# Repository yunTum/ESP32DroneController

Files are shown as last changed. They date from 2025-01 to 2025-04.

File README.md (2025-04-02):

# ESP32DroneController

## Debug Software


## Web Setting


## FlightAnalyzer


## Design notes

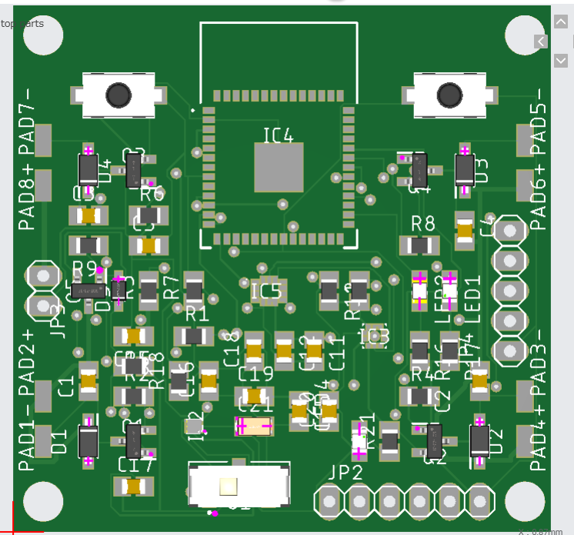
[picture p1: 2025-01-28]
schematic/ESPDroneV2/スクリーンショット 2025-01-21 234431.png

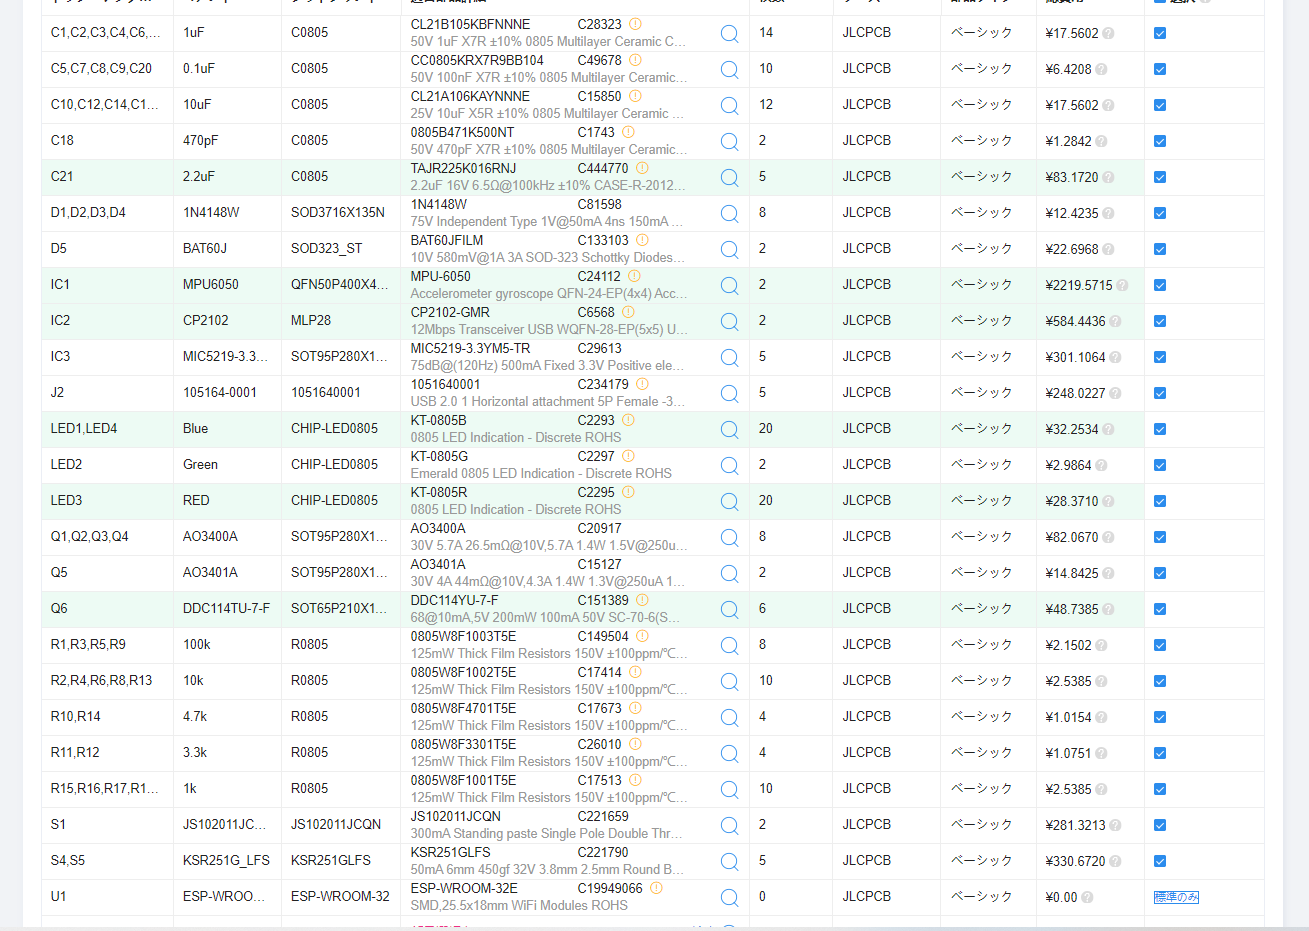
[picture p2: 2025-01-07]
schematic/esp32drone/スクリーンショット 2024-10-18 125452.png

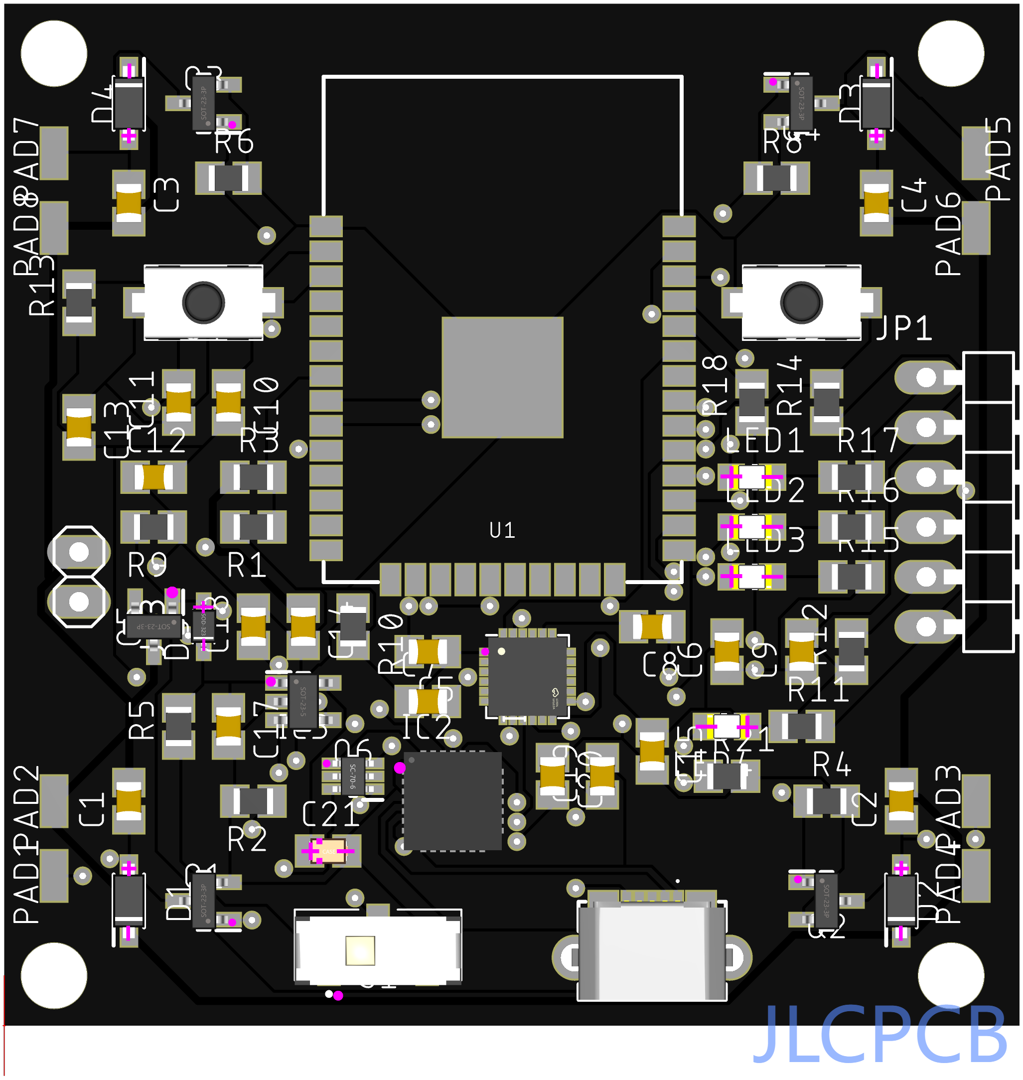
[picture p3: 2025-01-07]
schematic/esp32drone/capture-2024-10-16T03_43_27.196Z.png

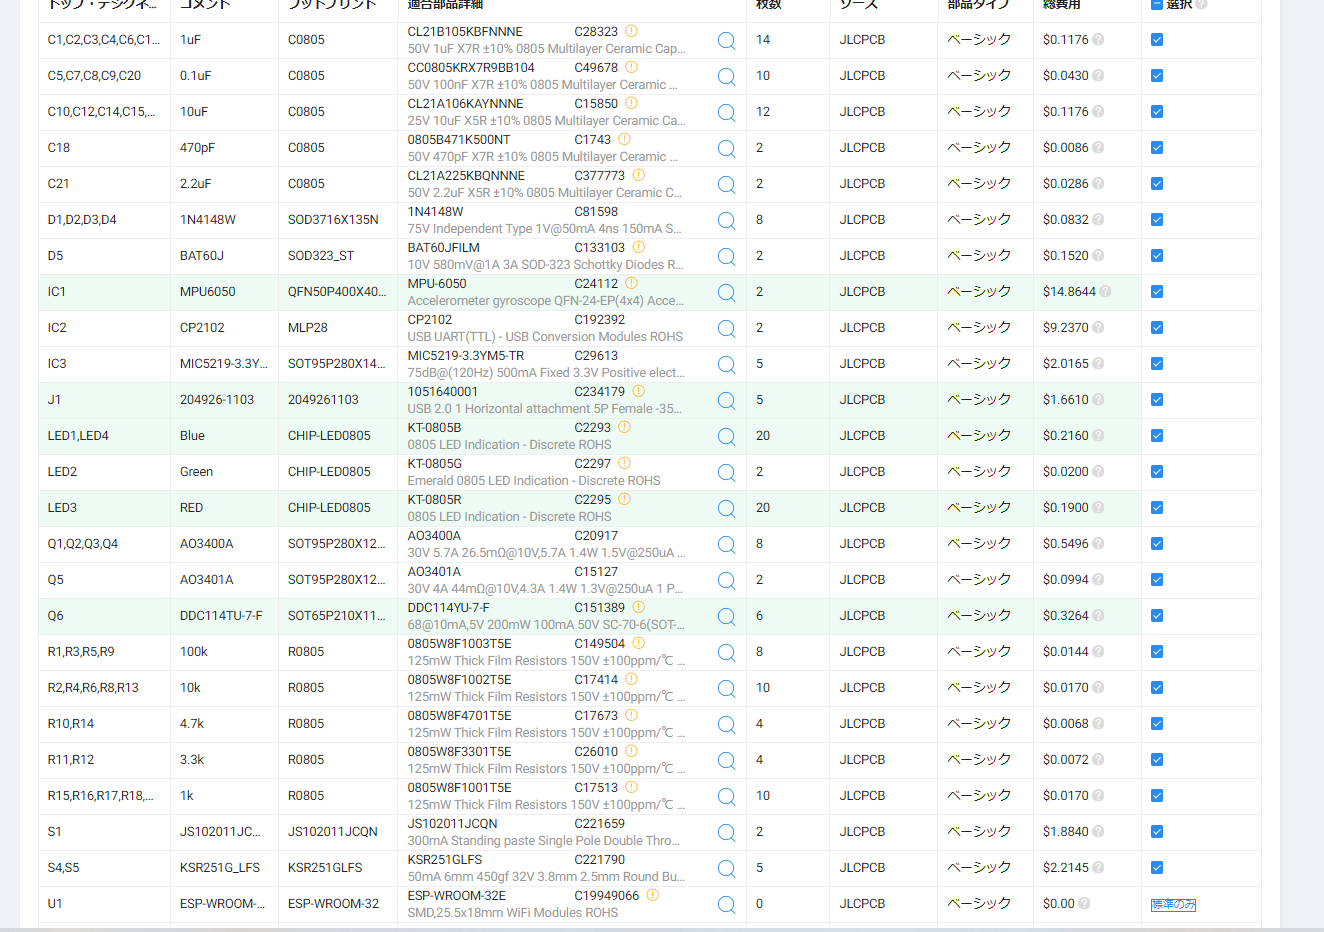
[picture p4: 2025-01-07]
schematic/esp32drone/スクリーンショット 2024-10-16 073514.png

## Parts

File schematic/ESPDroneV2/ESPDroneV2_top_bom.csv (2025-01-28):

Comment | Designator | Footprint | LCSC Part #
1N4148W | D1 D2 D3 D4 | SOD3716X135N
1k | R16 R17 R21 | R0805
1uF | C1 C2 C3 C4 C5 C11 C15 C17 C18 C19 | C0805
2.2uF | C21 | C0805
3.3k | R11 R12 | R0805
4.7k | R18 | R0805
10k | R2 R4 R6 R7 R8 | R0805
10uF | C14 C16 | C0805
100k | R1 R3 R5 R9 | R0805
100uF | C12 C20 | C0805
AO3400A | Q1 Q2 Q3 Q4 | SOT95P280X125-3N
AO3401A | Q5 | SOT95P280X125-3N
BAT60J | D5 | SOD323_ST
Blue | LED1 LED4 | CHIP-LED0805
ESP32-MINI-1-N4 | IC4 | ESP32MINI1N4
Green | LED2 | CHIP-LED0805
JS102011JCQN | S1 | JS102011JCQN
KSR251G_LFS | S2 S3 | KSR251GLFS
LPS22HHTR | IC3 | LPS22HHTR
LSM6DSLTR | IC5 | LSM6DSLTR
MOTOR1+ | PAD2+ | SMD1 27-2 54
MOTOR1- | PAD1- | SMD1 27-2 54
MOTOR2+ | PAD4+ | SMD1 27-2 54
MOTOR2- | PAD3- | SMD1 27-2 54
MOTOR3+ | PAD6+ | SMD1 27-2 54
MOTOR3- | PAD5- | SMD1 27-2 54
MOTOR4+ | PAD8+ | SMD1 27-2 54
MOTOR4- | PAD7- | SMD1 27-2 54
NCP176AMX330TCG | IC2 | NCP176AMX330TCG

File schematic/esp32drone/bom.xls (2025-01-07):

Comment | Designator | Footprint | JLCPCB Part #
1uF | C1,C2,C3,C4,C6,C11,C13,C16 | C0805 | C28323
DDC114TU-7-F | Q6 | SOT65P210X110-6N | C260942
56k | R7,R9,R13 | R0805 | C17756
Green | LED2 | CHIP-LED0805 | C84257
470pF | C18 | C0805 | C1743
MINI-USB-32005-201 | X1 | 32005-201 | C2681563
JS102011JCQN | S7 | JS102011JCQN | C221659
3.3k | R11,R12 | R0805 | C26010
RED | LED3 | CHIP-LED0805 | C84256
100k | R1,R3 | R0805 | C149504
10k | R2,R4,R6,R8 | R0805 | C17414
AO3401A | Q5 | SOT95P280X125-3N | C15127
Blue | LED1,LED4 | CHIP-LED0805 | C84259
AO3400A | Q1,Q2,Q3,Q4 | SOT95P280X125-3N | C344010
1k | R15,R16,R17,R18,R21 | R0805 | C17513
2.2nF | C8 | C0805 | C28260
10uF | C10,C12,C14,C15,C17,C19 | C0805 | C15850
4.7k | R10,R14 | R0805 | C17673
MPU6050 | IC1 | QFN50P400X400X95-25T265X275N | C24112
0.1uF | C5,C7,C9,C20 | C0805 | C49678
MIC5219-3.3YM5-TR | IC4 | SOT95P280X145-5N | C29613
BAT60J | D5 | SOD323_ST | C133103
ESP-WROOM-32 | U1 | ESP-WROOM-32 | C82899
CP2102 | IC2 | MLP28 | C192392
KSR251G_LFS | S4,S5 | KSR251GLFS | C221790
1N4148W | D1,D2,D3,D4 | SOD3716X135N | C81598

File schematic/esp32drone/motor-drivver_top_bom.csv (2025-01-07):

Comment | Designator | Footprint | LCSC Part #
0.1uF | C5 C7 C8 C9 C20 | C0805
1N4148W | D1 D2 D3 D4 | SOD3716X135N
1k | R15 R16 R17 R18 R21 | R0805
1uF | C1 C2 C3 C4 C6 C11 C13 | C0805
2.2uF | C21 | C0805
3.3k | R11 R12 | R0805
4.7k | R10 R14 | R0805
10k | R2 R4 R6 R8 R13 | R0805
10uF | C10 C12 C14 C15 C17 C19 | C0805
100k | R1 R3 R5 R9 | R0805
470pF | C18 | C0805
105164-0001 | J2 | 1051640001
AO3400A | Q1 Q2 Q3 Q4 | SOT95P280X125-3N
AO3401A | Q5 | SOT95P280X125-3N
BAT60J | D5 | SOD323_ST
Blue | LED1 LED4 | CHIP-LED0805
CP2102 | IC2 | MLP28
DDC114TU-7-F | Q6 | SOT65P210X110-6N
ESP-WROOM-32 | U1 | ESP-WROOM-32
Green | LED2 | CHIP-LED0805
JS102011JCQN | S1 | JS102011JCQN
KSR251G_LFS | S4 S5 | KSR251GLFS
MIC5219-3.3YM5-TR | IC3 | SOT95P280X145-5N
MOTOR1+ | PAD2 | SMD1 27-2 54
MOTOR1- | PAD1 | SMD1 27-2 54
MOTOR2+ | PAD4 | SMD1 27-2 54
MOTOR2- | PAD3 | SMD1 27-2 54
MOTOR3+ | PAD6 | SMD1 27-2 54
MOTOR3- | PAD5 | SMD1 27-2 54
MOTOR4+ | PAD8 | SMD1 27-2 54
MOTOR4- | PAD7 | SMD1 27-2 54
MPU6050 | IC1 | QFN50P400X400X95-25T265X275N
RED | LED3 | CHIP-LED0805

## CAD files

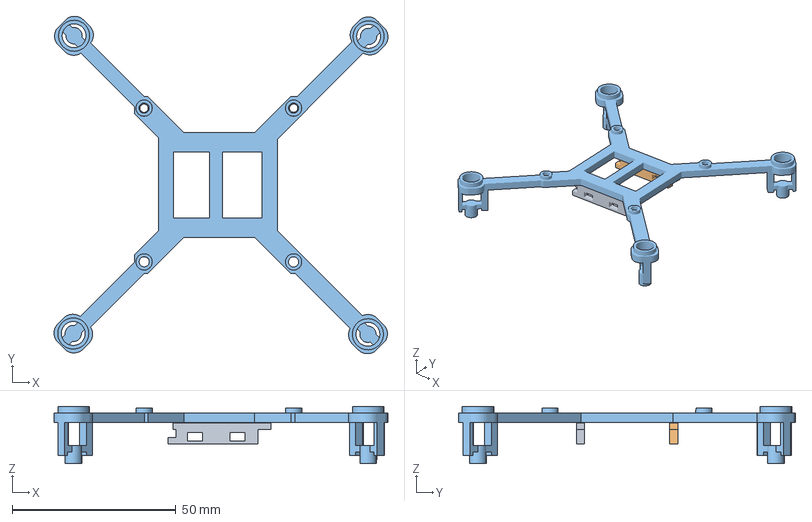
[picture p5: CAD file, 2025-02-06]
frame/ESPドローンフレームV6_SMALL v4.3mf
102.1 x 103.1 x 17.5 mm
ボディ36
ボディ59
ボディ86

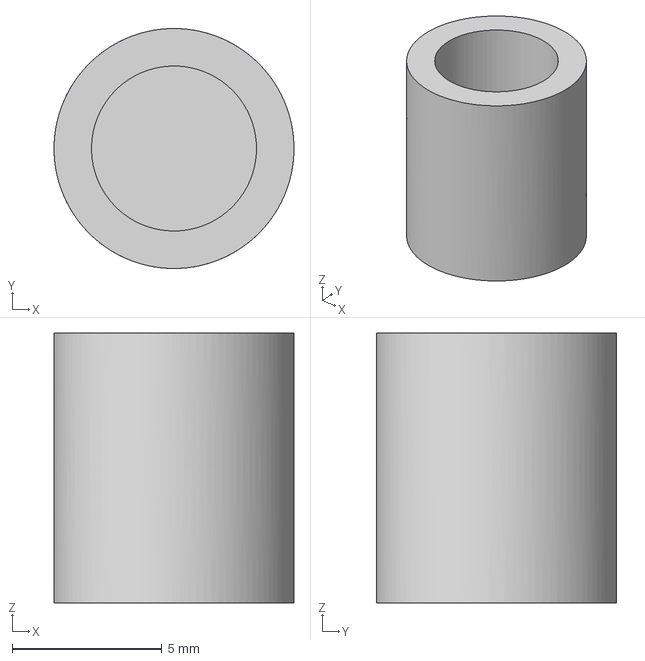
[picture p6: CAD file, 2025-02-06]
frame/offset_foot v2.3mf
8.00 x 8.00 x 9.00 mm

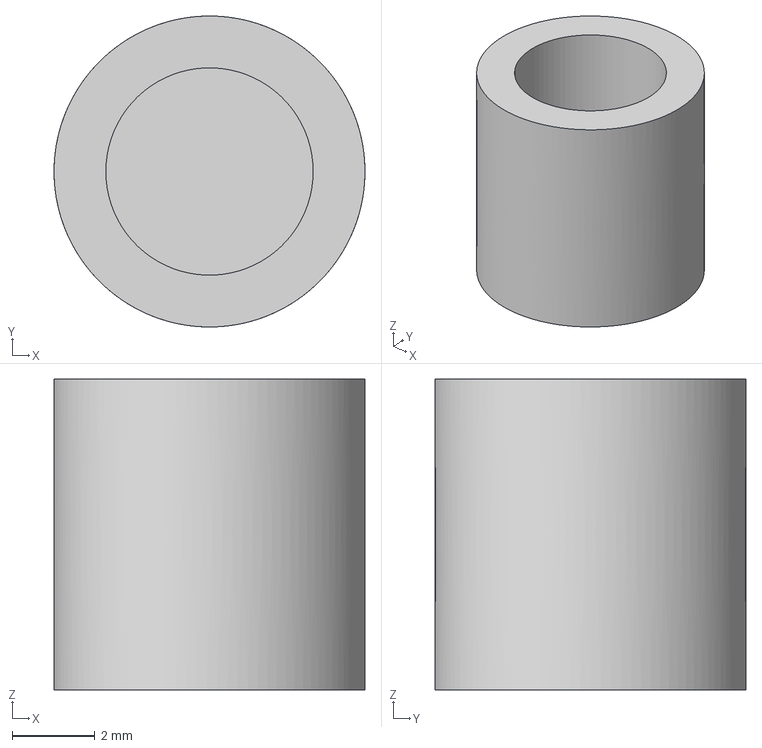
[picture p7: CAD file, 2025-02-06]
frame/offset_foot.3mf
7.50 x 7.50 x 7.50 mm

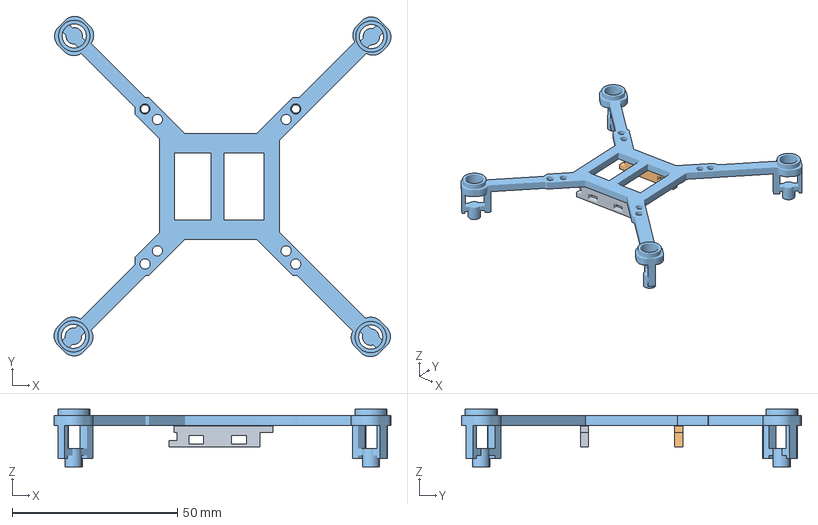
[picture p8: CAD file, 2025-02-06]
frame/ESPドローンV3フレーム v1.3mf
102.1 x 103.1 x 17.5 mm
ボディ36
ボディ59
ボディ86

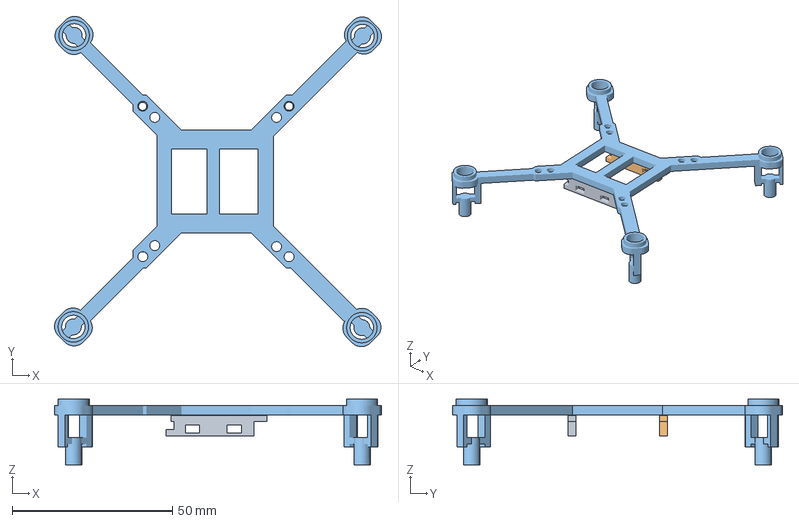
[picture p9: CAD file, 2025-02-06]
frame/ESPドローンV3フレーム v2.3mf
102.1 x 103.1 x 20.5 mm
ボディ36
ボディ59
ボディ86

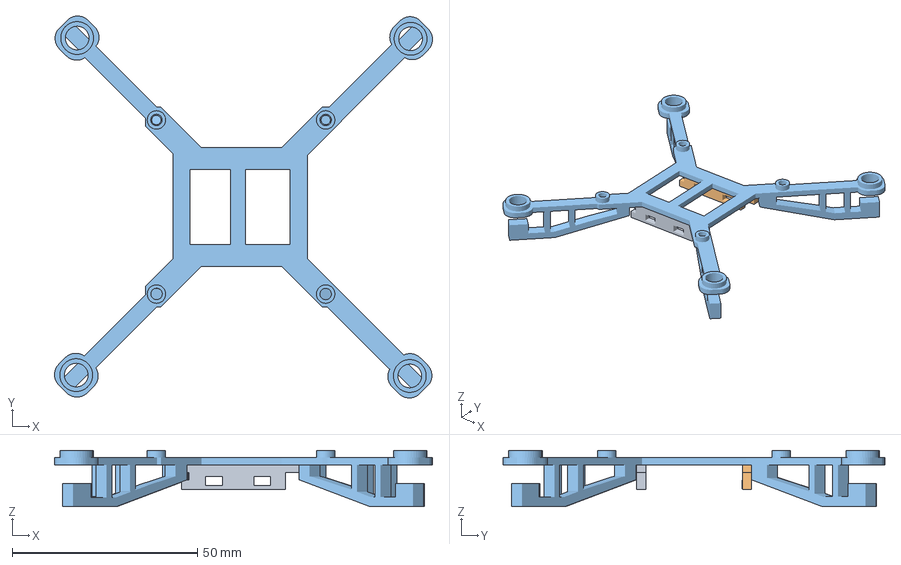
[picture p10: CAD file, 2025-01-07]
frame/ESPドローンフレームV5_SMALL v5.3mf
102.0 x 103.1 x 15.2 mm
ボディ36
ボディ59
ボディ86

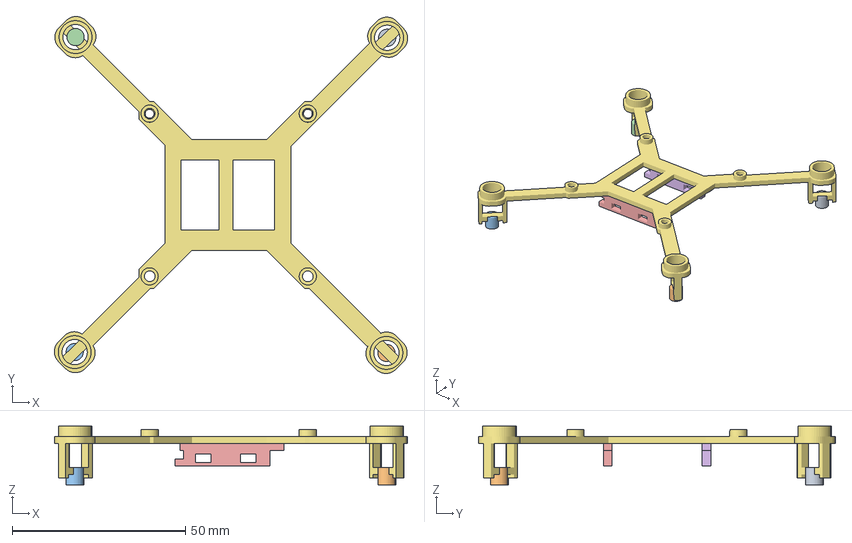
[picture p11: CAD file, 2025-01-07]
frame/ESPドローンフレームV6_SMALL v3.3mf
102.1 x 103.1 x 17.0 mm
ボディ107
ボディ108
ボディ109
ボディ110
ボディ36
ボディ59
ボディ86

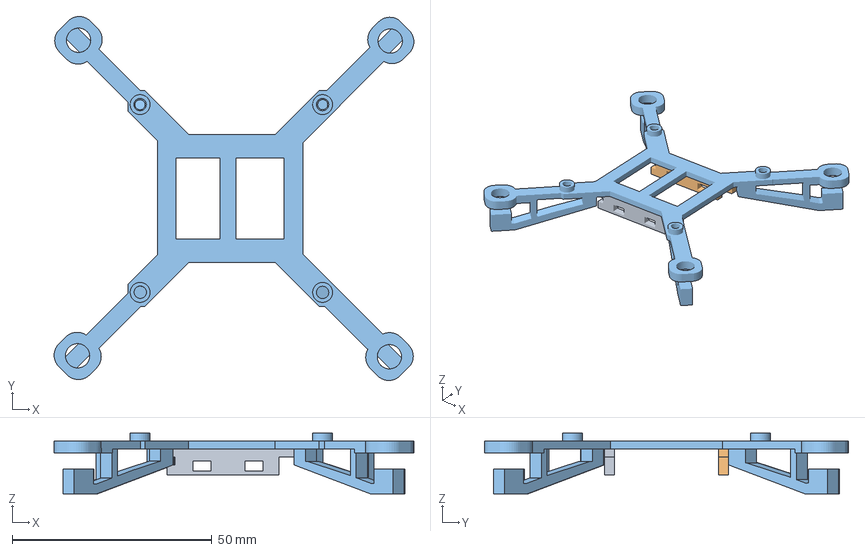
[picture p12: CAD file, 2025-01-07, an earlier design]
frame/ESPドローンフレームV5_SMALL v4.3mf
90.1 x 91.1 x 15.2 mm
ボディ36
ボディ59
ボディ62

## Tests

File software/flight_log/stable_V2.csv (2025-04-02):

timestamp | seqno | synctime | servo1 | servo2 | servo3 | servo4 | pid_roll | pid_pitch | pid_yaw | imu_roll | imu_pitch | imu_yaw | gyro_x | gyro_y | gyro_z | acc_x | acc_y | acc_z | battery | altitude | temperature | calculated_altitude
2025-04-03 00:18:51 | 78 | 41.539 | 0 | 0 | 0 | 0 | -0.05 | 0.05 | 0.00 | 0.06 | -0.06 | -0.03 | 0.00 | 0.00 | 0.00 | 0.00 | 0.00 | 40.95 | 3.47 | -0.16 | 26.30 | -10987.54
2025-04-03 00:18:51 | 85 | 53.829 | 0 | 0 | 0 | 0 | -0.05 | 0.05 | 0.00 | 0.06 | -0.06 | -0.03 | 0.00 | 0.00 | 0.00 | 0.00 | 0.00 | 40.93 | 3.47 | -0.08 | 26.30 | -27434.34
2025-04-03 00:18:51 | 86 | 8.774 | 0 | 0 | 0 | 0 | -0.05 | 0.05 | 0.00 | 0.06 | -0.06 | -0.03 | 0.00 | 0.00 | 0.00 | 0.00 | 0.00 | 40.93 | 3.47 | 0.16 | 26.30 | 32807.77
2025-04-03 00:18:52 | 87 | 29.254 | 0 | 0 | 0 | 0 | -0.05 | 0.05 | 0.00 | 0.06 | -0.06 | -0.03 | 0.00 | 0.00 | 0.00 | 0.00 | 0.00 | 40.93 | 3.47 | 0.28 | 26.29 | 5442.00
2025-04-03 00:18:52 | 88 | 49.734 | 0 | 0 | 0 | 0 | -0.05 | 0.05 | 0.00 | 0.06 | -0.06 | -0.03 | 0.00 | 0.00 | 0.00 | 0.00 | 0.00 | 40.91 | 3.47 | -0.75 | 26.30 | -21957.32
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

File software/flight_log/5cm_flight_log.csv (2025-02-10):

timestamp | seqno | servo1 | servo2 | servo3 | servo4 | pid_roll | pid_pitch | pid_yaw | imu_roll | imu_pitch | imu_yaw | gyro_x | gyro_y | gyro_z | acc_x | acc_y | acc_z | battery | altitude | temperature
2025-02-10 11:53:55 | 0 | 0 | 0 | 0 | 0 | 0.00 | 0.00 | 0.00 | 0.00 | 0.00 | 0.00 | 0.00 | 0.00 | 0.00 | 0.00 | 0.00 | 0.00 | 3.44 | 0.00 | 0.00
2025-02-10 11:53:55 | 1 | 0 | 0 | 0 | 0 | 0.00 | 0.00 | 0.00 | 0.00 | 0.00 | 0.00 | 0.00 | 0.00 | 0.00 | 0.00 | 0.00 | 0.00 | 3.40 | 0.00 | 0.00
2025-02-10 11:53:55 | 2 | 0 | 0 | 0 | 0 | 0.00 | 0.00 | 0.00 | 0.00 | 0.00 | 0.00 | 0.00 | 0.00 | 0.00 | 0.00 | 0.00 | 0.00 | 3.41 | 0.00 | 0.00
2025-02-10 11:53:55 | 3 | 0 | 0 | 0 | 0 | 0.00 | 0.00 | 0.00 | 0.00 | 0.00 | 0.00 | 0.00 | 0.00 | 0.00 | 0.00 | 0.00 | 0.00 | 3.41 | 0.00 | 0.00
2025-02-10 11:53:56 | 4 | 0 | 0 | 0 | 0 | 0.00 | 0.00 | 0.00 | 0.00 | 0.00 | 0.00 | 0.00 | 0.00 | 0.00 | 0.00 | 0.00 | 0.00 | 3.40 | 0.00 | 0.00
2025-02-10 11:53:56 | 7 | 0 | 0 | 0 | 0 | 0.00 | 0.00 | 0.00 | 0.00 | 0.00 | 0.00 | 0.00 | 0.00 | 0.00 | 0.00 | 0.00 | 0.00 | 3.41 | 0.00 | 0.00
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

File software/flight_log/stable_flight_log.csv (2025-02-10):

timestamp | seqno | servo1 | servo2 | servo3 | servo4 | pid_roll | pid_pitch | pid_yaw | imu_roll | imu_pitch | imu_yaw | gyro_x | gyro_y | gyro_z | acc_x | acc_y | acc_z | battery | altitude | temperature | calculated_altitude
2025-02-10 18:42:00 | 0 | 0 | 0 | 0 | 0 | 0.00 | 0.00 | 0.00 | 0.00 | 0.00 | 0.00 | 0.00 | 0.00 | 0.00 | 0.00 | 0.00 | 0.00 | 3.50 | 0.00 | 0.00 | 9245.58
2025-02-10 18:42:00 | 1 | 0 | 0 | 0 | 0 | 0.00 | 0.00 | 0.00 | 0.00 | 0.00 | 0.00 | 0.00 | 0.00 | 0.00 | 0.00 | 0.00 | 0.00 | 3.47 | 0.00 | 0.00 | 9242.97
2025-02-10 18:42:00 | 2 | 0 | 0 | 0 | 0 | 0.00 | 0.00 | 0.00 | 0.00 | 0.00 | 0.00 | 0.00 | 0.00 | 0.00 | 0.00 | 0.00 | 0.00 | 3.47 | 0.00 | 0.00 | 9217.43
2025-02-10 18:42:00 | 10 | 0 | 0 | 0 | 0 | 0.00 | 0.00 | 0.00 | 0.00 | 0.00 | 0.00 | 0.00 | 0.00 | 0.00 | 0.00 | 0.00 | 0.00 | 3.47 | 0.00 | 0.00 | 9215.71
2025-02-10 18:42:00 | 11 | 0 | 0 | 0 | 0 | 0.00 | 0.00 | 0.00 | 0.00 | 0.00 | 0.00 | 0.00 | 0.00 | 0.00 | 0.00 | 0.00 | 0.00 | 3.47 | 0.00 | 0.00 | 9206.49
2025-02-10 18:42:00 | 13 | 0 | 0 | 0 | 0 | 0.00 | 0.00 | 0.00 | 0.00 | 0.00 | 0.00 | 0.00 | 0.00 | 0.00 | 0.00 | 0.00 | 0.00 | 3.47 | 0.00 | 0.00 | 9205.38
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

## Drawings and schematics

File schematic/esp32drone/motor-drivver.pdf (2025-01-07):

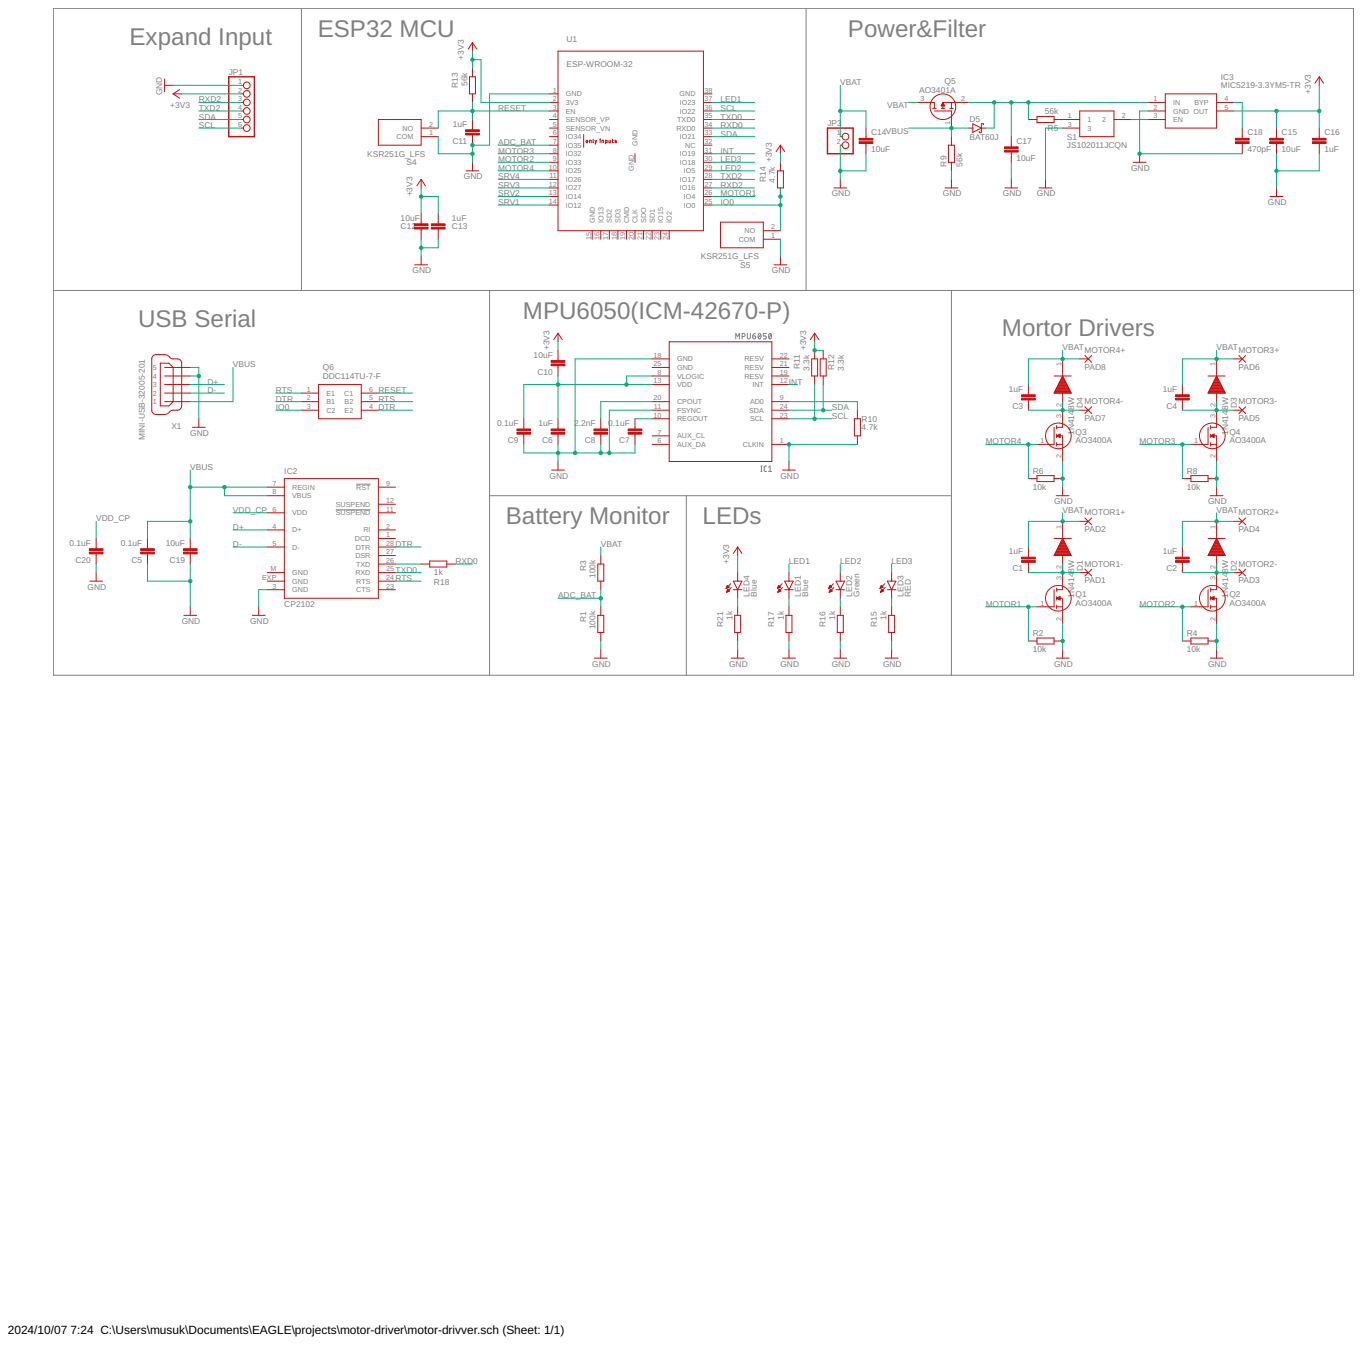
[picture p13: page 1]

2024/10/07 7:24 C:\Users\musuk\Documents\EAGLE\projects\motor-driver\motor-drivver.sch (Sheet: 1/1)

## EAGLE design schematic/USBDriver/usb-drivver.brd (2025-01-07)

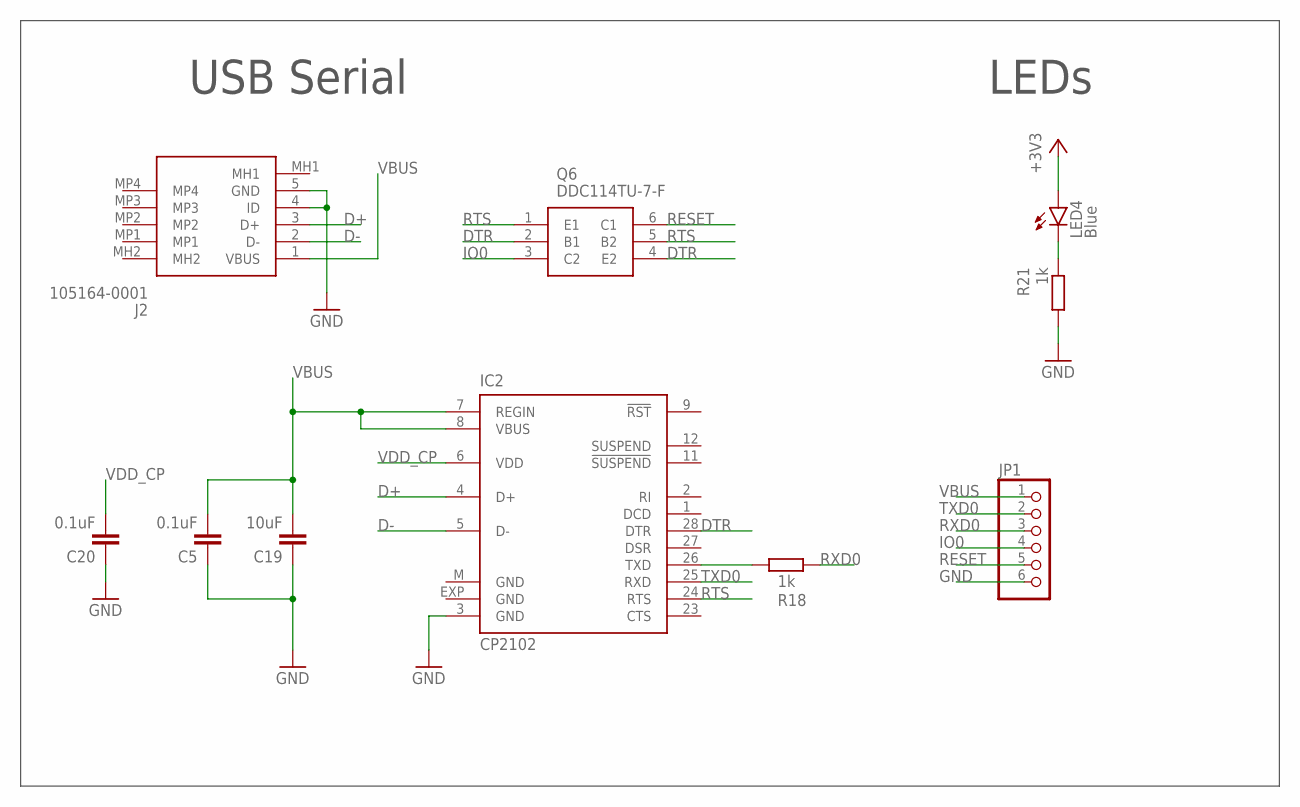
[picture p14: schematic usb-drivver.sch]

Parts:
C5, C20: 0.1uF; C0805
C19: 10uF; C0805
IC2: CP2102; MLP28
J2: 105164-0001; 1051640001
JP1: PINHD-1X6; 1X06
LED4: Blue; CHIP-LED0805
Q6: DDC114TU-7-F; SOT65P210X110-6N
R18, R21: 1k; R0805

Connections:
+3V3: LED4.A
D+: IC2.4 (D+), J2.3 (D+)
D-: IC2.5 (D-), J2.2 (D-)
DTR: IC2.28 (DTR), Q6.2 (B1), Q6.4 (E2)
GND: C5.1, C19.1, C20.1, IC2.3 (GND), IC2.EXP (GND), IC2.M (GND), J2.4 (ID), J2.5 (GND), JP1.6, R21.2
IO0: JP1.4, Q6.3 (C2)
unnamed: IC2.26 (TXD), R18.1
unnamed: LED4.C, R21.1
RESET: JP1.5, Q6.6 (C1)
RTS: IC2.24 (RTS), Q6.1 (E1), Q6.5 (B2)
RXD0: JP1.3, R18.2
TXD0: IC2.25 (RXD), JP1.2
VBUS: C5.2, C19.2, IC2.7 (REGIN), IC2.8 (VBUS), J2.1 (VBUS), JP1.1
VDD_CP: C20.2, IC2.6 (VDD)

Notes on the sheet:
USB Serial
LEDs

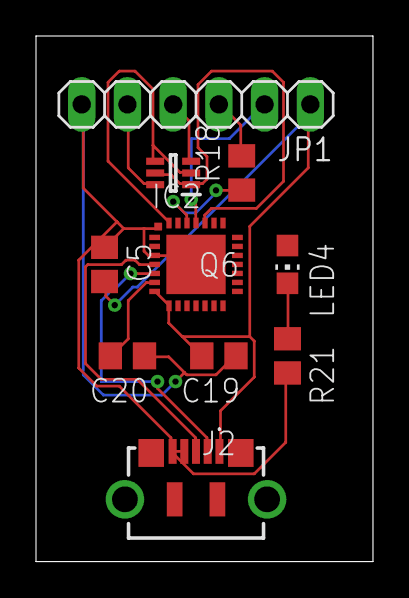
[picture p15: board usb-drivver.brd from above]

Board: 2 copper layers, 18.7 x 29.2 mm, 10 parts (0 on the bottom side), 13 nets.

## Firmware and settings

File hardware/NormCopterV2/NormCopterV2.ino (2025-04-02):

/*
UPDATE MARK 20240108
*/
#include <WiFi.h>
#include <WebServer.h>
#include "Arduino.h"
#include <EEPROM.h>
#include <esp_wifi.h>
#include <esp_bt.h>
#include <esp_pm.h>
#include <Wire.h>

WebServer server(80);

const char* ssid = "****************";
const char* password = "****************";

#define MINTHROTTLE 50
#define CALSTEPS 256 // gyro and acc calibration steps
enum ang { ROLL,PITCH,YAW };
#define THR 2 // thro position is rc_value array

#define EEPROM_SIZE 64
#define LED_YELLOW 23
#define LED_RED 18
#define LED_GREEN 5
#define ADC_BAT 35
#define LOW_VOLT 3.0
#define CS_PIN 27
String act_ip;

extern void initMot();
extern int16_t rcValue[];

#define LoopInterval 4 // minimum 2ms
const float dt = 0.001 * float(LoopInterval); //in sec 
unsigned long synctime;    

void setup() 
{
  Wire.begin(21, 22);  // SDA=21, SCL=22 (ESP32のデフォルトピン)
  // Wire.setClock(400000); // 400kHz I2C
  Wire.setClock(100000);  // 100kHzに設定

  EEPROM.begin(EEPROM_SIZE);  
  Serial.begin(115200);
  pinMode(ADC_BAT, INPUT);
  pinMode(LED_YELLOW, OUTPUT);
  // pinMode(LED_RED, OUTPUT);
  pinMode(LED_GREEN, OUTPUT);
  pinMode(CS_PIN, OUTPUT);
  digitalWrite(CS_PIN, HIGH);
  digitalWrite(LED_YELLOW, LOW);
  delay(3000);
  
  // Init Modules
  initMot();
  LSM6DSLTR_init();
  readacc();

  LPSHHTR_init();
  // Wi-Fi connection
  WiFi.mode(WIFI_STA);
  WiFi.setSortMethod(WIFI_CONNECT_AP_BY_SIGNAL);
  WiFi.setScanMethod(WIFI_ALL_CHANNEL_SCAN);
  WiFi.begin(ssid, password);
  while (WiFi.status() != WL_CONNECTED) 
  {
    delay(500);
    Serial.print(".");
  }
  Serial.println();
  act_ip = WiFi.localIP().toString().c_str();
  Serial.println(act_ip);

  delay(200);
  init_RC(); 
  server.on("/", handleCmd);
  server.begin();
  Serial.println("HTTP server started");
    
  Serial.println("T - Timing");
  Serial.println("R - RC");
  Serial.println("r - Raw RC");
  Serial.println("G - Gyro raw");
  Serial.println("g - Gyro filt");
  Serial.println("A - Accel raw");
  Serial.println("M - Madgwick");
  Serial.println("P - PID");
  Serial.println("S - Servo");
  Serial.println("B - Battery");
  Serial.println("H - LPS22HH");
  Serial.println("L - Logging");
  Serial.println("W - PID Settings");

  synctime = millis() + LoopInterval;
  digitalWrite(LED_GREEN, LOW);
  // digitalWrite(LED_YELLOW, LOW);
}

bool armed, fmode, led, calibrateRequest;

float GyroX,GyroY,GyroZ;
float AccX, AccY, AccZ;

extern int16_t gyroADC[3];
extern int16_t accADC[3];
extern float roll_IMU, pitch_IMU, yaw_IMU;
extern float roll_PID, pitch_PID, yaw_PID;
extern float roll_des, pitch_des, yaw_des;
extern float roll_rc, pitch_rc, yaw_rc;
// extern float throttle;
extern int16_t axisPID[3];
extern uint16_t servo[];

extern float pressure, temperature, altitude;

unsigned long oldT;
float B_gyro = 0.1;
char debugvalue;
float battery_vol = 0.0;
int counter = 0;
int sendInterval = 20;

bool isHeader = true;
const int LOG_INTERVAL = 20; // 何回のループに1回ログを取るか
int logCounter = 0;
bool isDetailLog = false;

extern float Kp_rate, Ki_rate, Kd_rate;
extern float Kp_yaw, Ki_yaw, Kd_yaw;
extern float Kp_ang, Ki_ang, Kd_ang;
extern float Kp_ayw, Ki_ayw, Kd_ayw;

void loop() 

{ 
  float gx,gy,gz;
  battery_vol = getBattery();
  if (debugvalue == 'B') showBatteryVol(battery_vol);
  
  // parser part
  if (Serial.available()) 
  {
    char ch = Serial.read();
    if (ch != 10) debugvalue = ch;
  }
  if (debugvalue == 'T') Serial.println(micros() - oldT);
  
  server.handleClient();
  while (millis() < synctime) delay(1);
  synctime += LoopInterval;
  
  if (debugvalue == 'T') oldT = micros();
  
  //des -> thr 0..+300; ang -90..+90
  rcvalCyclic();

  if (debugvalue == 'R') 
    Serial.printf("%4.0f %4.0f %4.0f  %d  %d  %d  %d\n", roll_rc, pitch_rc, yaw_rc, armed, fmode, led, calibrateRequest);  
  
  roll_des  = roll_rc;
  pitch_des = pitch_rc;
  yaw_des   = yaw_rc;
  
  if (calibrateRequest) {
    calibrateRequest = false;
    Serial.println("Calibrate Request");
    calibrate();
  }
  
  GyroAcc_getADC(); // 550us instead of 680us

  // gx = float(gyroADC[0]); 
  // gy = float(gyroADC[1]); 
  // gz = float(gyroADC[2]); 

  // GyroX = gx;
  // GyroY = gy;
  // GyroZ = gz;

  // // 1g=4096 -> 0.000244
  // AccX = float(accADC[0]);  
  // AccY = float(accADC[1]);  
  // AccZ = float(accADC[2]);

  if (debugvalue == 'G') 
    Serial.printf("%4d %4d %4d \n", gyroADC[0], gyroADC[1], gyroADC[2]);
  if (debugvalue == 'A') 
    Serial.printf("%5d %5d %5d \n", accADC[0], accADC[1], accADC[2]);
  getLPS22HH();

  if (debugvalue == 'H') 
    Serial.printf("Pressure: %6.2f Temp: %5.2f Alt: %6.2f \n", pressure, temperature, altitude);

  if (debugvalue == 'g') 
    Serial.printf("%4.0f %4.0f %4.0f \n", GyroX, GyroY, GyroZ);
  if (debugvalue == 'a') 
    Serial.printf("%4.0f %4.0f %4.0f \n", AccX, AccY, AccZ);

  Madgwick6DOF(GyroX,GyroY,GyroZ,AccX,AccY,AccZ,dt);
  if (debugvalue == 'M') 
    Serial.printf("%4.0f %4.0f %4.0f \n", roll_IMU, pitch_IMU, yaw_IMU);

  // fmode = true; // test
  if (fmode) {
    controlANG();
  } else {
    controlStable();
  }
  controlRATE();
  
  if (led) digitalWrite(LED_YELLOW, HIGH);
  else      digitalWrite(LED_YELLOW, LOW);

  if (debugvalue == 'P') Serial.printf("%4.0f %4.0f %4.0f \n", roll_PID, pitch_PID, yaw_PID);

  axisPID[ROLL]  = 10.0*roll_PID;
  axisPID[PITCH] = 10.0*pitch_PID;
  axisPID[YAW]   = 10.0*yaw_PID;
  if (counter == sendInterval) {
    sendDroneData();
    counter = 0;
  }

  // ロギング開始/停止のコマンドを追加
  if (debugvalue == 'L') {
    logCounter = 0;
    if(isHeader) {
      // ヘッダー行を送信

      Serial.println("DATA,gyroADC_X,gyroADC_Y,gyroADC_Z,accADC_X,accADC_Y,accADC_Z,GyroX,GyroY,GyroZ,AccX,AccY,AccZ,roll_IMU,pitch_IMU,yaw_IMU,roll_PID,pitch_PID,yaw_PID");
    }
    isHeader = false;
    // データロギング
    if(logCounter++ % LOG_INTERVAL == 0) {
      if (isDetailLog) {
        Serial.printf("DATA,%d,%d,%d,%d,%d,%d,%.2f,%.2f,%.2f,%.2f,%.2f,%.2f,%.2f,%.2f,%.2f,%.2f,%.2f,%.2f,%.2f\n",
          gyroADC[0], gyroADC[1], gyroADC[2],
          accADC[0], accADC[1], accADC[2],
          GyroX, GyroY, GyroZ,
          AccX, AccY, AccZ,
          roll_IMU, pitch_IMU, yaw_IMU,
          roll_PID, pitch_PID, yaw_PID);
      }
      else {
        Serial.printf("%.2f,%.2f,%.2f,%.2f,%.2f,%.2f\n",
          GyroX, GyroY, GyroZ,
          roll_PID, pitch_PID, yaw_PID);
      }
    }
  }

  if (debugvalue == 'W') {
      Serial.println("--------------------------------");
      Serial.println("Rate Settings");
      Serial.println("Kp_rate: " + String(Kp_rate));
      Serial.println("Ki_rate: " + String(Ki_rate));
      Serial.println("Kd_rate: " + String(Kd_rate));
      Serial.println("Yaw Settings");
      Serial.println("Kp_yaw: " + String(Kp_yaw));
      Serial.println("Ki_yaw: " + String(Ki_yaw));
      Serial.println("Kd_yaw: " + String(Kd_yaw));
      Serial.println("Ang Settings");
      Serial.println("Kp_ang: " + String(Kp_ang));
      Serial.println("Ki_ang: " + String(Ki_ang));
      Serial.println("Kd_ang: " + String(Kd_ang));
      Serial.println("Ang-Yaw Settings");
      Serial.println("Kp_ayw: " + String(Kp_ayw));
      Serial.println("Ki_ayw: " + String(Ki_ayw));
      Serial.println("Kd_ayw: " + String(Kd_ayw));
      Serial.println("--------------------------------");
      
      debugvalue = ' ';
  }

  counter++;
  mix();
  if (debugvalue == 'S') Serial.printf("%4d %4d %4d %4d\n", servo[0], servo[1], servo[2], servo[3]);
  // calib only !
  /*
  /**/
  // if (LOW_VOLT > battery_vol) {
  //   // digitalWrite(LED_GREEN, LOW);
  //   digitalWrite(LED_RED, HIGH);
  //   servo[0] = 0; servo[1] = 0; servo[2] = 0; servo[3] = 0; 
  // } else {
  //   // digitalWrite(LED_GREEN, HIGH);
  //   digitalWrite(LED_RED, LOW);
  // }
  writeMot();
}

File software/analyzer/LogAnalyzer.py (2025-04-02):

import pandas as pd
import matplotlib.pyplot as plt
import numpy as np
from pathlib import Path
import matplotlib.dates as mdates
from datetime import datetime
from PyQt5.QtWidgets import (QApplication, QMainWindow, QWidget, QVBoxLayout, 
                           QHBoxLayout, QPushButton, QLabel, QFileDialog, 
                           QComboBox, QMessageBox, QScrollArea, QTabWidget)
from PyQt5.QtCore import Qt
from matplotlib.backends.backend_qt5agg import FigureCanvasQTAgg as FigureCanvas
import sys

def analyze_log(file_path):
    # CSVファイルを読み込む
    df = pd.read_csv(file_path)
    
    # 基本的な統計情報を表示
    print("\n基本統計情報:")
    print(df.describe())
    
    # プロットの設定
    plt.rcParams['figure.figsize'] = [12, 6]
    plt.rcParams['grid.alpha'] = 0.3
    plt.rcParams['grid.color'] = '#cccccc'
    
    # IMUの角度データをプロット
    plt.figure()
    plt.plot(df['roll_IMU'], label='Roll')
    plt.plot(df['pitch_IMU'], label='Pitch')
    plt.plot(df['yaw_IMU'], label='Yaw')
    plt.title('IMU Angles')
    plt.xlabel('Sample')
    plt.ylabel('Angle (deg)')
    plt.legend()
    plt.grid(True)
    
    # PIDの出力をプロット
    plt.figure()
    plt.plot(df['roll_PID'], label='Roll PID')
    plt.plot(df['pitch_PID'], label='Pitch PID')
    plt.plot(df['yaw_PID'], label='Yaw PID')
    plt.title('PID Outputs')
    plt.xlabel('Sample')
    plt.ylabel('Output')
    plt.legend()
    plt.grid(True)
    
    # ジャイロデータをプロット
    plt.figure()
    plt.plot(df['GyroX'], label='X')
    plt.plot(df['GyroY'], label='Y')
    plt.plot(df['GyroZ'], label='Z')
    plt.title('Gyro Data')
    plt.xlabel('Sample')
    plt.ylabel('Angular Velocity (deg/s)')
    plt.legend()
    plt.grid(True)
    
    # 加速度データをプロット
    plt.figure()
    plt.plot(df['AccX'], label='X')
    plt.plot(df['AccY'], label='Y')
    plt.plot(df['AccZ'], label='Z')
    plt.title('Accelerometer Data')
    plt.xlabel('Sample')
    plt.ylabel('Acceleration (m/s²)')
    plt.legend()
    plt.grid(True)
    
    # 全てのグラフを表示
    plt.show()
    
    # 追加の統計情報
    print("\nIMU角度の平均値:")
    print(f"Roll: {df['roll_IMU'].mean():.2f}°")
    print(f"Pitch: {df['pitch_IMU'].mean():.2f}°")
    print(f"Yaw: {df['yaw_IMU'].mean():.2f}°")
    
    print("\nPID出力の標準偏差:")
    print(f"Roll: {df['roll_PID'].std():.2f}")
    print(f"Pitch: {df['pitch_PID'].std():.2f}")
    print(f"Yaw: {df['yaw_PID'].std():.2f}")

def analyze_phase(df):
    # IMUとPIDの相関を計算
    roll_corr = np.correlate(df['roll_IMU'], df['roll_PID'], mode='full')
    pitch_corr = np.correlate(df['pitch_IMU'], df['pitch_PID'], mode='full')
    yaw_corr = np.correlate(df['yaw_IMU'], df['yaw_PID'], mode='full')
    
    # IMUとPIDの比較プロット（正規化して表示）
    plt.figure(figsize=(15, 15))  # サイズを大きくして4つのサブプロットを配置
    
    # Roll
    plt.subplot(3, 1, 1)
    roll_imu_norm = df['roll_IMU'] / df['roll_IMU'].abs().max()
    roll_pid_norm = df['roll_PID'] / df['roll_PID'].abs().max()
    gyro_x_norm = df['GyroX'] / df['GyroX'].abs().max()
    plt.plot(gyro_x_norm, label='Gyro X (normalized)')
    # plt.plot(roll_imu_norm, label='Roll IMU (normalized)')
    plt.plot(roll_pid_norm, label='Roll PID (normalized)')

    # plt.plot(roll_imu_norm + roll_pid_norm, label='Combined', alpha=0.5)
    plt.plot(gyro_x_norm + roll_pid_norm, label='Combined', alpha=0.5)
    # plt.title('Roll: IMU vs PID (Normalized)')
    plt.title('Roll: Gyro X vs PID (Normalized)')

    plt.legend()
    plt.grid(True)
    
    # Pitch
    plt.subplot(3, 1, 2)
    pitch_imu_norm = df['pitch_IMU'] / df['pitch_IMU'].abs().max()
    pitch_pid_norm = df['pitch_PID'] / df['pitch_PID'].abs().max()
    gyro_y_norm = df['GyroY'] / df['GyroY'].abs().max()

    plt.plot(gyro_y_norm, label='Gyro Y (normalized)')
    # plt.plot(pitch_imu_norm, label='Pitch IMU (normalized)')
    plt.plot(pitch_pid_norm, label='Pitch PID (normalized)')
    plt.plot(gyro_y_norm + pitch_pid_norm, label='Combined', alpha=0.5)

    # plt.plot(pitch_imu_norm + pitch_pid_norm, label='Combined', alpha=0.5)
    # plt.title('Pitch: IMU vs PID (Normalized)')
    plt.title('Pitch: Gyro Y vs PID (Normalized)')
    plt.legend()
    plt.grid(True)
    

    # Yaw
    plt.subplot(3, 1, 3)
    yaw_imu_norm = df['yaw_IMU'] / df['yaw_IMU'].abs().max()
    yaw_pid_norm = df['yaw_PID'] / df['yaw_PID'].abs().max()
    gyro_z_norm = df['GyroZ'] / df['GyroZ'].abs().max()
    plt.plot(gyro_z_norm, label='Gyro Z (normalized)')

    # plt.plot(yaw_imu_norm, label='Yaw IMU (normalized)')
    plt.plot(yaw_pid_norm, label='Yaw PID (normalized)')
    plt.plot(gyro_z_norm + yaw_pid_norm, label='Combined', alpha=0.5)
    # plt.plot(yaw_imu_norm + yaw_pid_norm, label='Combined', alpha=0.5)

    # plt.title('Yaw: IMU vs PID (Normalized)')
    plt.title('Yaw: Gyro Z vs PID (Normalized)')
    plt.legend()
    plt.grid(True)
    

    # # 合成波形の比較
    # plt.subplot(4, 1, 4)
    # plt.plot(roll_imu_norm + roll_pid_norm, label='Roll Combined', alpha=0.7)
    # plt.plot(pitch_imu_norm + pitch_pid_norm, label='Pitch Combined', alpha=0.7)
    # plt.plot(yaw_imu_norm + yaw_pid_norm, label='Yaw Combined', alpha=0.7)
    # plt.title('Combined Waveforms Comparison')
    # plt.legend()
    # plt.grid(True)
    
    plt.tight_layout()
    plt.show()
    
    # 相関係数と合成波形の統計を計算
    print("\nIMUとPIDの相関係数（-1に近いほど良い）:")
    print(f"Roll: {df['GyroX'].corr(df['roll_PID']):.3f}")
    print(f"Pitch: {df['GyroY'].corr(df['pitch_PID']):.3f}")
    print(f"Yaw: {df['GyroZ'].corr(df['yaw_PID']):.3f}")

    print("\n合成波形の統計:")
    print("Roll合成波形の標準偏差:", (gyro_x_norm + roll_pid_norm).std().round(3))
    print("Pitch合成波形の標準偏差:", (gyro_y_norm + pitch_pid_norm).std().round(3))
    print("Yaw合成波形の標準偏差:", (gyro_z_norm + yaw_pid_norm).std().round(3))
    
    # 位相差の評価
    def calculate_phase_difference(imu, pid):
        correlation = np.correlate(imu, pid, mode='full')
        max_corr_index = np.argmax(np.abs(correlation))
        phase_diff = max_corr_index - len(imu)
        return phase_diff
    
    print("\n位相差（サンプル数）:")
    print(f"Roll: {calculate_phase_difference(gyro_x_norm, roll_pid_norm)}")
    print(f"Pitch: {calculate_phase_difference(gyro_y_norm, pitch_pid_norm)}")
    print(f"Yaw: {calculate_phase_difference(gyro_z_norm, yaw_pid_norm)}")
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

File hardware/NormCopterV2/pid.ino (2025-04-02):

float Kp_rate = 0.20;    //P-gain - rate mode
float Ki_rate = 0.01;    //I-gain - rate mode
float Kd_rate = 0.01;   //D-gain - rate mode 
float Kp_yaw  = 0.19;    //Yaw P-gain
float Ki_yaw  = 0.01;    //Yaw I-gain
float Kd_yaw  = 0.02;    //Yaw D-gain 

float Kp_ang  = 0.60;    //Ang P-gain
float Ki_ang  = 0.01;    //Ang I-gain
float Kd_ang  = 0.01;    //Ang D-gain
float Kp_ayw  = 0.20;    //Ang Yaw P-gain
float Ki_ayw  = 0.01;    //Ang Yaw I-gain
float Kd_ayw  = 0.07;    //Ang Yaw D-gain

float thro_des, roll_des, pitch_des, yaw_des; // RC input 0 to 1
float roll_rate_des, pitch_rate_des, yaw_rate_des; // Desired rate commands
float error_roll, integral_roll, integral_roll_prev, derivative_roll;
float error_pitch,integral_pitch,integral_pitch_prev,derivative_pitch;
float error_yaw,  integral_yaw,  integral_yaw_prev,  derivative_yaw;
float error_roll_prev, error_pitch_prev, error_yaw_prev;
float GyroX_prev, GyroY_prev, GyroZ_prev;
float integral_ang_roll,  integral_ang_roll_prev;
float integral_ang_pitch, integral_ang_pitch_prev;
float integral_ang_yaw,   integral_ang_yaw_prev;

float roll_PID = 0;
float pitch_PID = 0;
float yaw_PID = 0;

float i_limit = 5.0; 
extern int16_t rcValue[];

float pid_limit = 50;


// Stableモード用のPIDゲイン
// float Kp_stable = 1.3;     // 水平維持用の比例ゲイン
// float Ki_stable = 0.04;    // 水平維持用の積分ゲイン
// float Kd_stable = 0.02;    // 水平維持用の微分ゲイン
float Kp_stable = 0.14;     // 水平維持用の比例ゲイン
float Ki_stable = 0.01;    // 水平維持用の積分ゲイン
float Kd_stable = 0.00;    // 水平維持用の微分ゲイン
// float Kp_stable = 1.46;     // 水平維持用の比例ゲイン
// float Ki_stable = 0.40;    // 水平維持用の積分ゲイン
// float Kd_stable = 0.20;    // 水平維持用の微分ゲイン

// Stableモード用の積分項
float integral_stable_roll = 0;
float integral_stable_pitch = 0;
float prev_stable_roll_error = 0;
float prev_stable_pitch_error = 0;

#define MAX_ANGLE 25.0     // 最大傾斜角（度）
#define STABLE_I_LIMIT 10.0 // 積分項の制限

float filtered_roll_IMU = 0;
float filtered_pitch_IMU = 0;
float filtered_yaw_IMU = 0;

#define ANGLE_FILTER 0.95  // 角度フィルタの係数
#define D_FILTER_STABLE 0.8    // 微分項用フィルター係数
#define D_FILTER_RATE 0.8    // 微分項用フィルター係数
#define FILTER_GAIN 0.95    // フィルター係数

void controlStable() 
{
  // 角度のフィルタリング
  // filtered_roll_IMU = filtered_roll_IMU * ANGLE_FILTER + roll_IMU * (1 - ANGLE_FILTER);
  // filtered_pitch_IMU = filtered_pitch_IMU * ANGLE_FILTER + pitch_IMU * (1 - ANGLE_FILTER);

  // ロール角の制御（水平に戻す）
  float roll_error = 0 - roll_IMU;  // 目標角度は0度（水平）
  integral_stable_roll += roll_error * dt;
  integral_stable_roll = constrain(integral_stable_roll, -STABLE_I_LIMIT, STABLE_I_LIMIT);
  float roll_D = (roll_error - prev_stable_roll_error) / dt;
  // roll_D = roll_D * (1 - D_FILTER_STABLE) + prev_roll_D * D_FILTER_STABLE;

  // スティック入力との組み合わせ
  float stick_roll = roll_rc * MAX_ANGLE;  // スティック入力を角度に変換
  stick_roll = 0;
  roll_des = stick_roll + (Kp_stable * roll_error + 
                          Ki_stable * integral_stable_roll + 
                          Kd_stable * roll_D);
  
  // ピッチ角の制御（水平に戻す）
  float pitch_error = 0 - pitch_IMU;  // 目標角度は0度（水平）
  integral_stable_pitch += pitch_error * dt;
  integral_stable_pitch = constrain(integral_stable_pitch, -STABLE_I_LIMIT, STABLE_I_LIMIT);
  float pitch_D = (pitch_error - prev_stable_pitch_error) / dt;
  // pitch_D = pitch_D * (1 - D_FILTER_STABLE) + prev_pitch_D * D_FILTER_STABLE;

  // スティック入力との組み合わせ
  float stick_pitch = pitch_rc * MAX_ANGLE;  // スティック入力を角度に変換
  stick_pitch = 0;
  pitch_des = stick_pitch + (Kp_stable * pitch_error + 
                            Ki_stable * integral_stable_pitch + 
                            Kd_stable * pitch_D);
                            
  // ヨー制御（通常のレートモード）
  // yaw_des = yaw_rc * 180.0;  // ヨーレートの目標値（度/秒）
  yaw_des = 0;
  
  // 前回値の保存
  prev_stable_roll_error = roll_error;
  prev_stable_pitch_error = pitch_error;
  
  // スロットルが低い場合は積分項をリセット
  if (rcValue[THR] < MINTHROTTLE) {
    integral_stable_roll = 0;
    integral_stable_pitch = 0;
  }
  
  // 角度制限
  // roll_des = constrain(roll_des, -MAX_ANGLE, MAX_ANGLE);
  // pitch_des = constrain(pitch_des, -MAX_ANGLE, MAX_ANGLE);
}

void controlANG() 
{
  // deg err
  error_roll  = roll_des  - roll_IMU; 
  integral_ang_roll = integral_ang_roll_prev + error_roll*dt;
  if (rcValue[THR] < MINTHROTTLE) integral_ang_roll = 0;
  integral_ang_roll = constrain(integral_ang_roll, -i_limit, i_limit); 
  float roll_rate_command = Kp_ang * error_roll +
                           Ki_ang * integral_ang_roll -
                           Kd_ang * GyroX;
  roll_rate_des = roll_rate_command;
  integral_ang_roll_prev = integral_ang_roll;
  

  error_pitch = pitch_des - pitch_IMU;
  integral_ang_pitch = integral_ang_pitch_prev + error_pitch*dt;
  if (rcValue[THR] < MINTHROTTLE) integral_ang_pitch = 0;
  integral_ang_pitch = constrain(integral_ang_pitch, -i_limit, i_limit); 
  float pitch_rate_command = Kp_ang * error_pitch +
                           Ki_ang * integral_ang_pitch -
                           Kd_ang * GyroY;
  pitch_rate_des = pitch_rate_command;
  integral_ang_pitch_prev = integral_ang_pitch;



  error_yaw = yaw_des - yaw_IMU;
  integral_ang_yaw = integral_ang_yaw_prev + error_yaw*dt;
  if (rcValue[THR] < MINTHROTTLE) integral_ang_yaw = 0;
  integral_ang_yaw = constrain(integral_ang_yaw, -i_limit, i_limit); 
  float yaw_rate_command = Kp_ayw * error_yaw +
                           Ki_ayw * integral_ang_yaw -
                           Kd_ayw * GyroZ;
  yaw_rate_des = yaw_rate_command;

  integral_ang_yaw_prev = integral_ang_yaw;
  
  if (debugvalue == 'p')
  {
    Serial.print(error_yaw);        Serial.print("  ");
    //Serial.print(integral_ang_yaw); Serial.print("  ");
    Serial.print(GyroZ);   Serial.print("  ");
    Serial.print(yaw_des); Serial.println();     
  }
}
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

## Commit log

2024-10-11 RC値の変更
2024-12-01 fix contoller
    上書きされていたのを修正
2025-01-07 add sch
    [ESPDroneV2.brd, ESPDroneV2.sch, bom.xls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]
2025-01-07 add frame
    [ESPドローンフレームV5_SMALL v4.3mf, ESPドローンフレームV5_SMALL v5.3mf, ESPドローンフレームV6_SMALL v3.3mf]
2025-01-28 add LED
2025-01-28 add V2 schematic
    [ESPDroneV2_top_bom.csv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]
2025-02-06 add analyzer
    [drone_log_20250203_175545.csv, drone_log_20250203_175907.csv, drone_log_20250203_180203.csv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]
2025-02-06 update frame
    [ESPドローンV3フレーム v1.3mf, ESPドローンV3フレーム v2.3mf, ESPドローンフレームV6_SMALL v4.3mf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]
2025-02-10 update pid&esc
2025-02-10 update flight-analyzer
    [5cm_flight_log.csv, stable_flight_log.csv]
2025-02-12 update pid& add alt
2025-03-14 add filter
2025-04-02 update software
    [stable_V2.csv]
